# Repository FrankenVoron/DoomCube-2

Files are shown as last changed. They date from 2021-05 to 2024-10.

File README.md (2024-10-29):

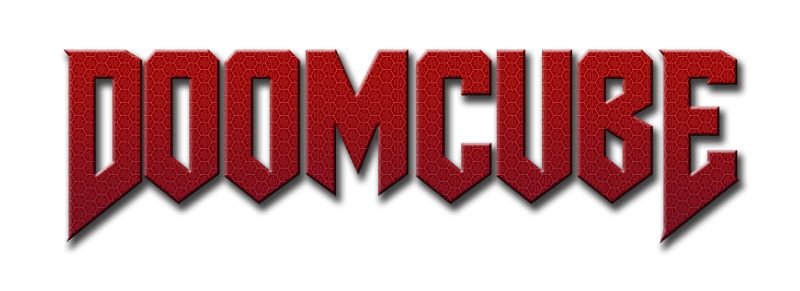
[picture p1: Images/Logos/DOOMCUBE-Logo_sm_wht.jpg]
DOOMCUBE

# Doom-Cube
A mod for Voron 2.4; designed by the Voron community, for the Voron community! Please note that it is a work in progress, design iterations are expected. The files are hosted on github so we have a log of the past history for the parts.



#### Key features:

- 4040 vertical components to allow for insulation with air gap stock

- Top mounted Z drives

- Top mounted low voltage components

- Bottom mounted high voltage components

#### Optional

- Replace X/Y cable chains with umbelical (Z chain retained for A/B motors and Y endstop)

#### Changes required:

- 4pcs 4040 extrusions (HFSB5-4040)   -or-   4pcs 404020 rounded extrusions (HFSR5-404020)

- New Z Idlers  (only printed parts required)

- Relocate X/Y endstops  (only printed parts required)

- Cable Glands for Umbelical

#### Tips for printing parts:

For any Voron stock parts, or the Z idlers, please use standard Voron settings.

For skirts, etc, you may use other settings to reduce filament usage. Currently I am using: 0.3mm layer height, 2 perimeters, 2 bottom, 3 top, 20% infill. 

## BOM 

All extrusions are listed using Misumi part numbers.

Part numbers are listed for both square 4040, and rounded 404020 vertical extrusions.  Choose only one type.  The first set of part numbers is for plain cut extrusions.  The second part number is for square extrusions that are cut and drilled by misumi.  

#### Note:
If you choose to use rounded corners, you will need to reuse your frame's existing 2020 vertical extrusions, or purchase a set of them for a scratch build.  The rounded verticals do not require machining, but the 2020 verticals that nest into them will need to have holes drilled to enable securing the rounded piece with blind joints, as shown here.

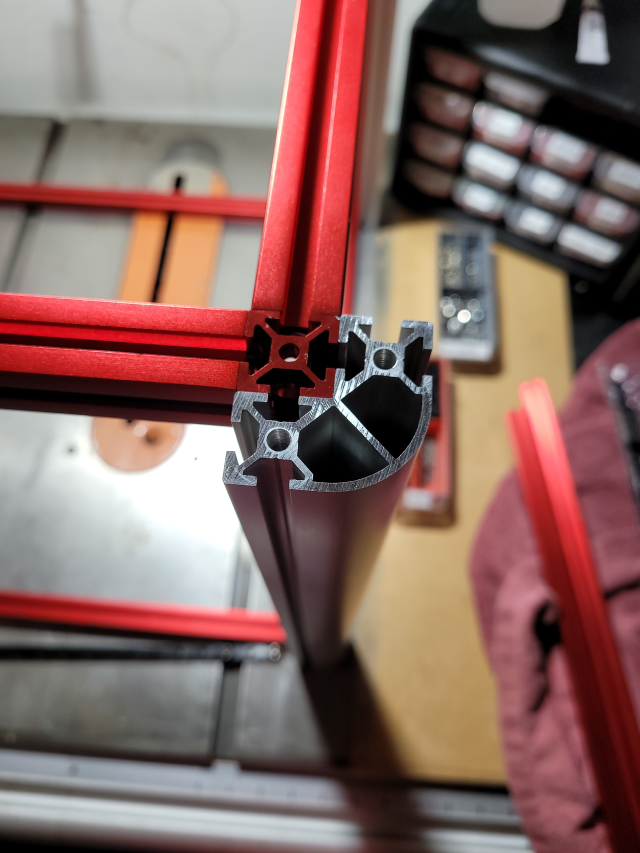
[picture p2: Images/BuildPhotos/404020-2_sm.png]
Corner extrusion profile shown from above


## Extrusions Based on Standard V2 Build Sizes

## DOOM-350
### Frame Extrusions
#### DIY
Misumi Part #  |Qty
|:----:|:----:|
Square Verticals: HFSB5-4040-530 |4 
Rounded Verticals: HFSR5-404020-530 |4

#### Pre-Drilled
Misumi Part #  |Qty
|:----:|:----:|
Square Verticals: HFSB5-4040-530-LCP-RCP |4

### Door Extrusions

#### DIY
Misumi Part #  |Qty
|:----:|:----:|
HFSB5-2020-530|2
HFSB5-2020-428|2

#### Pre-Drilled
Misumi Part #  |Qty
|:----:|:----:|
HFSB5-2020-530-AH10-BH520|2
HFSB5-2020-428-TPW|2

## DOOM-300
### Frame Extrusions
#### DIY
Misumi Part #  |Qty
|:----:|:----:|
Square Verticals: HFSB5-4040-480 |4
Rounded Verticals: HFSR5-404020-480 |4

#### Pre-Drilled
Misumi Part #  |Qty
|:----:|:----:|
Verticals: HFSB5-4040-480-LCP-RCP |4

### Door Extrusions
#### DIY
Misumi Part #  |Qty
|:----:|:----:|
HFSB5-2020-480|2
HFSB5-2020-378|2

#### Pre-Drilled
Misumi Part #  |Qty|
|:----:|:----:|
HFSB5-2020-480-AH10-BH470|2
HFSB5-2020-378-TPW|2

## DOOM-250
### Frame Extrusions
#### DIY
Misumi Part #  |Qty
|:----:|:----:|
Square Verticals: HFSB5-4040-430 |4
Rounded Verticals: HFSR5-404020-430 |4

#### Pre-Drilled
Misumi Part #  |Qty|
|:----:|:----:|
Square Verticals: HFSB5-4040-430-LCP-RCP| 4

### Door Extrusions

#### DIY
Misumi Part #  |Qty| 
|:----:|:----:|
HFSB5-2020-430|2
HFSB5-2020-328|2

#### Pre-Drilled

Misumi Part #  |Qty| 
|:----:|:----:|
HFSB5-2020-430-AH10-BH420|2
HFSB5-2020-328-TPW|2

## Door Hinges
Silver and Black are listed 

|Misumi Part #  |Qty|Color
|:---:|:---:|:---:|
HHPSN5-SET|2| Silver
HHPBSN5-SET|2| Black

# Ongoing and Future Development
While we all have many irons in the fire, Doomcube v2 is still being worked on.  Keep an eye out for changes coming to the panel printed parts, as well as some coming mods from the community.  In the interest of encouraging more Doom builds, as well as more mods, a complete DOOM CAD file is now available with all the Doom and Voron components together.  Find it in the CAD folder with all the individual component CAD files.  The individual components have been gone through and all hole sizes have been made consistent.  Missing chamfers were added, and some geometry cleaned up.  The frame and panel assemblies will stay as they are until new files are ready.
### CAD Notes
If you examine the complete CAD file you will see it is not limited to the basic DOOM and Voron components.  Included are two optional gantry variants, with a handful of popular community produced V2 mods installed.  The file is structured to be very easy to see what you want, and hide what you don't.  The step file has everything shown by default, so you'll need to hide the frame, skirts, and gantries you don't wish to see.  It should only take a few clicks.

DoomCubing is a great way to improve your v2.  It's also a perfect time to install several mods, while you have things partially disassembled.  To give you some ideas about possible mod combos, the optional modded gantries in the complete cad file contain the following excellent mods:

### Afterburner MGN12 Gantry
Mod|Repository
|:---:|:---:|
Ark's MGN12|https://github.com/VoronDesign/VoronUsers/tree/master/printer_mods/arkeet/mgn12
Hartk's GE5C Spherical Z Joint|[https://github.com/VoronDesign/VoronUsers/tree/main/printer_mods/hartk1213/Voron2.4_GE5C](https://mods.vorondesign.com/details/eB5T2RNQcYI4o6cilhpXEg)
Hartk's Pinmod (X/Y Joints, ,A/B Drive Frames, A/B idlers, Z idlers)|[https://github.com/hartk1213/MISC/tree/main/Voron%20Mods/Voron%202/2.4/Voron2.4_Pins_Mod](https://mods.vorondesign.com/details/C8XJJ0fBGfBFKQZctjKeA)

### Mantis MGN12 Gantry
Mod|Repository
|:---:|:---:|
Long's Mantis Toolhead|https://github.com/VoronDesign/VoronUsers/tree/master/printer_mods/Long/Mantis_Dual_5015
Hartk's GE5C Spherical Z Joint|[https://github.com/VoronDesign/VoronUsers/tree/main/printer_mods/hartk1213/Voron2.4_GE5C](https://mods.vorondesign.com/details/eB5T2RNQcYI4o6cilhpXEg)
Hartk's Pinmod (X/Y Joints, ,A/B Drive Frames, A/B idlers, Z idlers)|[https://github.com/hartk1213/MISC/tree/main/Voron%20Mods/Voron%202/2.4/Voron2.4_Pins_Mod](https://mods.vorondesign.com/details/C8XJJ0fBGfBFKQZctjKeA)
Phalanx's Other Idlers|https://github.com/selliott79/Other-V2-Idlers

### Other Mods
The following mods are present in all or most Doomcube variants in the complete CAD file.  Klicky is not on the Mantis toolhead, since it has a native magprobe that works identically to Klicky.

Mod|Repository
|:---:|:---:|
L.e.o.p.a.r.d and Hartk's Sexbolt Z Endstop|[https://github.com/hartk1213/MISC/tree/main/Voron%20Mods/Voron%202/2.4/Voron2.4_SexBolt_ZEndstop](https://mods.vorondesign.com/details/t1DBVlcUBbdEK6habEsVzg)
josar's Klicky Probe|https://github.com/jlas1/Klicky-Probe 
whoppingpochard's Gantry Rail Backers|https://github.com/tanaes/whopping_Voron_mods/tree/main/extrusion_backers

#### A big thanks to all original authors for permission to include their mods in the Doomcube CAD!  Always follow the links to their respective repos for the latest stl's, and info on how to best make use of their mods.

##### A set of stl checklists to match these mod sets is in the works.  That can be one of the most confusing parts of building up a modded printer from scratch, or doing many mods at once with redundant components.  Hopefully a few checklists will simplify things a little bit.  A huge debt is owed to all the mod makers and their willingness to share their work!  Keep up the good work y'all!

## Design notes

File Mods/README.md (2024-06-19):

# Mods

Printer mods for DOOMCUBE
Remember to update this README when uploading new mod!

## Table structure

Update the following table with the information about your mod:
- Your name
- A link to your sub-folder
- A short description of your mod

like so:
`
| Creator | [Mod title](link) | Description |`

---

| Creator | Mod title | Description |
| --- | --- | --- |
| crag-h4k | [direct drive z](./crag-h4k/direct-drive-z) |Replaces z motor assembly with a minimized direct drive z motor unit. |
| crag-h4k | [galileo adxl345 chain replacement](./crag-h4k/galileo-adxl345-chain-replacement) |Replaces the Galileo extruders's chain mount with a dedicated mount for a adxl345. |
| crag-h4k | [lil a drive cable cover](./crag-h4k/lil-a-drive-cable-cover) | Replaces beefy a-drive cable cover with a cute little cover - use with top mounted cable gland. |
| crag-h4k | [mgn12 galileo compatible cable gland mount](./crag-h4k/mgn12-galileo-cable-gland) | Simple cable gland mount for mgn12 x-axis mod and Galileo extruder. |
| crag-h4k | [z chain m12 gland ptfe anchor](./crag-h4k/z-chain-cable-gland-ptfe-anchor) | Simple a cable gland mount and 4mm PTFE tube pass-through for upper Z chain anchor - attempts to preserve z-axis build volume.  |
| mvieleers | [My Custom DoomCube-2](./mvieleers/my_doomcube) | 300m3 DoomCube-2 with several popular included and a few of my own mods. |
| mvieleers | [Schaffner FN-286 Plug Panel](./mvieleers/fn-286_plug_panel) | Modded Plug Panel to hold the Schafnner FN-286|
| mvieleers | [Corner Panel Mounts](./mvieleers/corner_panel_mounts)| Modded upper and lower corner caps and square feet to attach the top and bottom deck panels to the feet with magnets. |
| mvieleers | [Galileo ADXL345 Chain Replacement with Umbilical Mount](./mvieleers/adxl_mount_w_umbilical)| This mod is an alteration of crag-h4k's mod to replace the chain mount on a Galileo extruder with an adxl345 mount. The adxl345 mount has cutouts so an umbilical can be mounted to the adxl345 mount with tie-wraps.
| KayosMaker | [tip-in swing-in panels](./KayosMaker/Toolless%20Panel%20Mod) | Work In Progress - nothing now, just a frame generator and some shaved corner pieces.  will post the rest soon |
| MartinNYHC | [Slotted skirts with fan mount](./MartinNYHC/Slotted_Skirts_With_Fan_Mount) | 350m3 Doomcube slotted skirts with fan mount |
| TheSquiffy | [Side panels with more clearance](./TheSquiffy/Side_panels_with_more_clearance) | Side panels with more clearance for Doomcube |
| Maker Technologies | [Rounded Upper Corner Panel Mounts with Rubber Feet Support](./Maker_Technologies/Upper%20Rounded%20Corner%20Panel%20holder%20with%20Support%20for%20Rubber%20Feet) | Keeps the Top panel in place while adding a spot to insert rubber feet on the top corners.|
| Maker Technologies | [Rounded Lower Corner Panel Mounts](./Maker_Technologies/Lower%20Rounded%20Corner%20Panel%20Holder) | Keeps the bottom panel in place.|
| Maker Technologies | [BTT Pi TFT70 Mount](./Maker_Technologies/Pi%20Tft70%20Skirt%20Mount) | A mount for a BTT Pi TFT70 to attach to a skirt.|
| k3vOOoOO | [https://www.printables.com/model/604933-doomcube-dual-power-switch-plate](https://www.printables.com/model/604933-doomcube-dual-power-switch-plate)| Dual BOM-spec rocker switches and filtered inlet. |

---

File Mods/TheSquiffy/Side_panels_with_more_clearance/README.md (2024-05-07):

**Side panels with more clearance for DoomCube**

Original panel's distance it's set around 1.6mm, this sometimes gives few clearance for gantry's belts to move, scratching the panels and causing some noise during operation.

The purpose of this mod it's to reduce distance between the side panels from ~9.6mm down to 3.5mm, leaving up to 7mm clearance for belts.

This mod could also be applied to back panels even though it's not strictly necessary.

The design fills gaps between the extrusion bars and panels to avoid having small channels where dirt could end up.

I have personally installed to my DoomCube 250 and made 300 and 350 stl files but I couldn't test them directly.

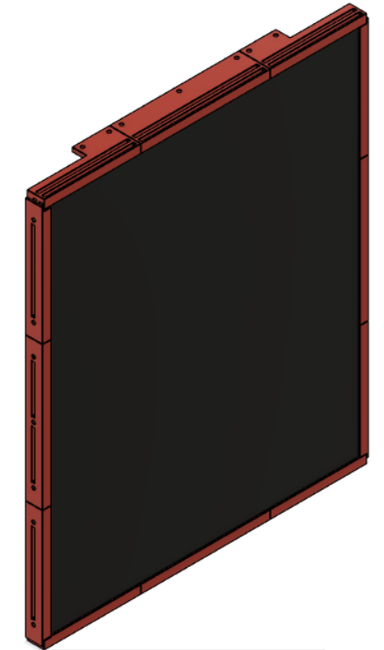
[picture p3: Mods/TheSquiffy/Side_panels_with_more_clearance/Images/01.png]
||
-

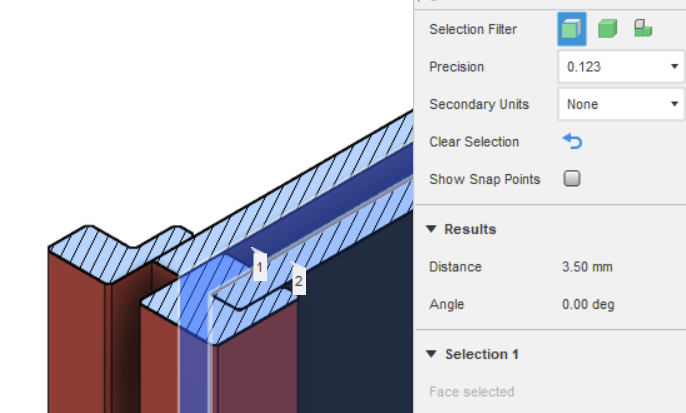
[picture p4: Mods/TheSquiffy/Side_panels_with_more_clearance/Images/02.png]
||
-

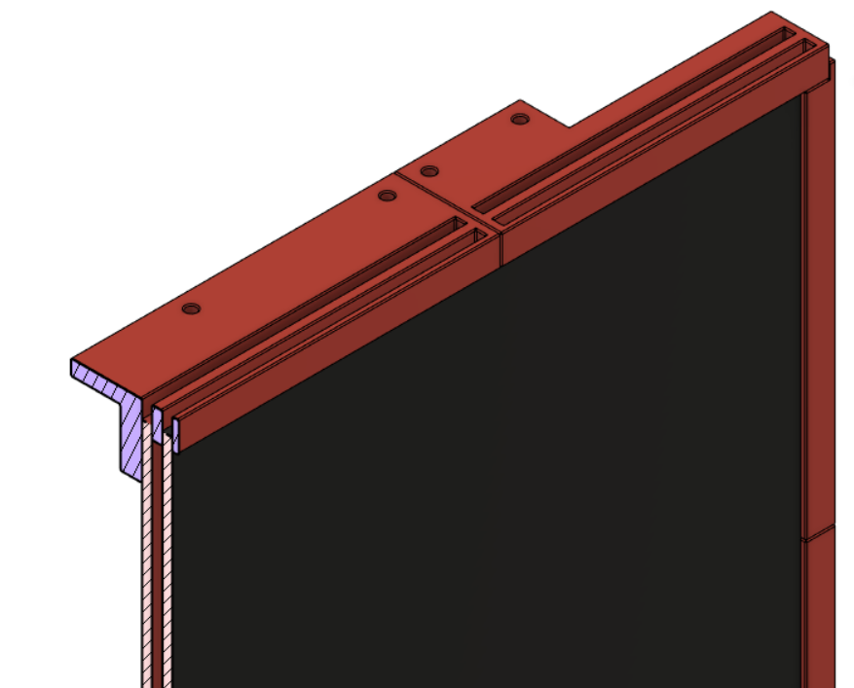
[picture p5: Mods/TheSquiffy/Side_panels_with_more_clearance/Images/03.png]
||
-

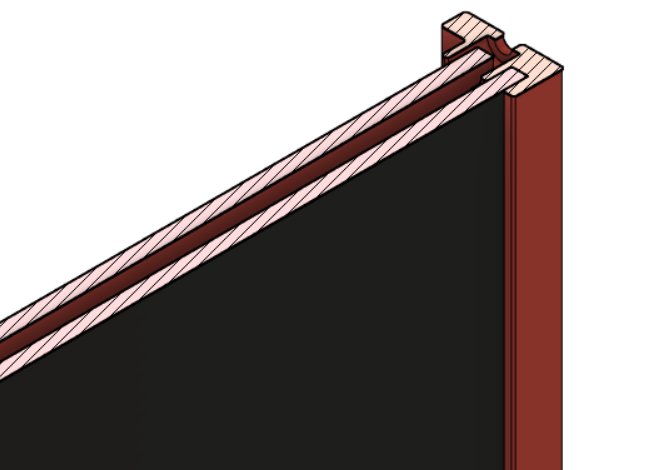
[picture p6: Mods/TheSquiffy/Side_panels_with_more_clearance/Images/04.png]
||
-

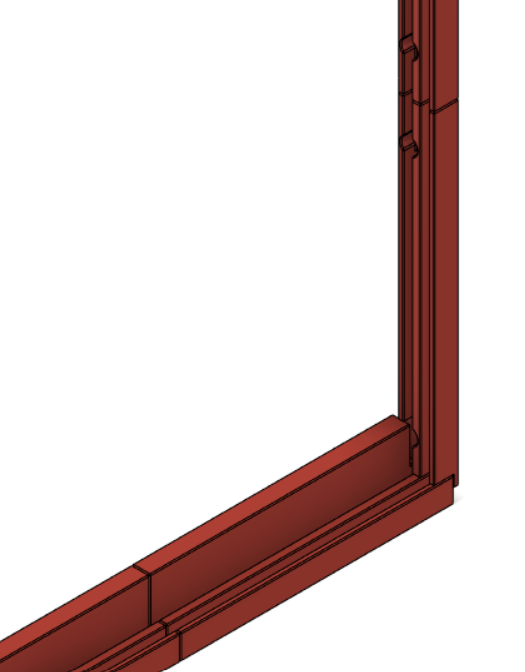
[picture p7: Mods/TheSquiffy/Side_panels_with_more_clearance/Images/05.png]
||
-

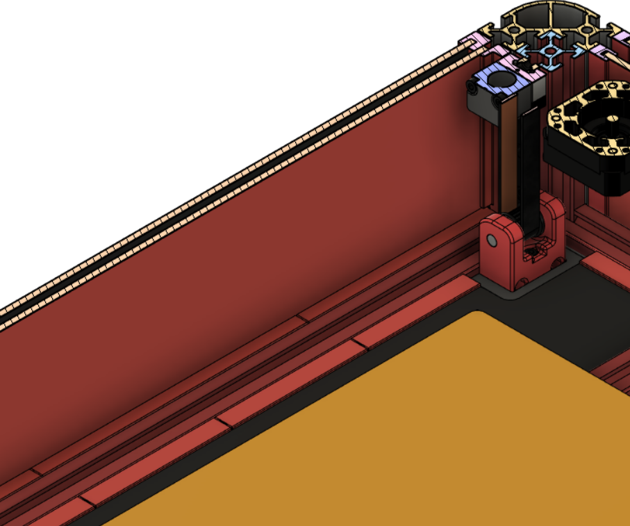
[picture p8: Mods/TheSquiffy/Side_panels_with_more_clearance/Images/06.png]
||
-

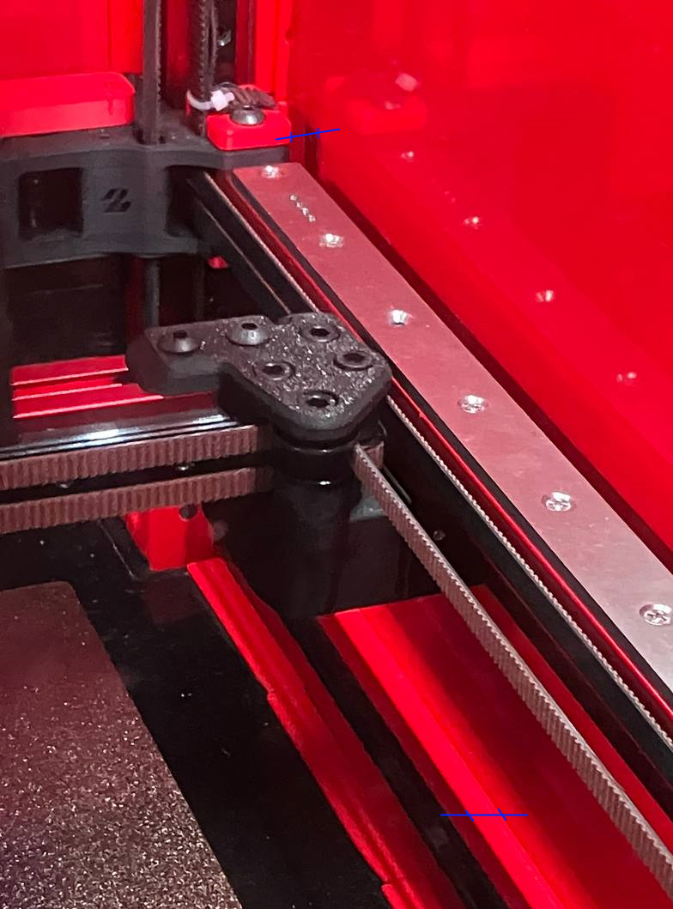
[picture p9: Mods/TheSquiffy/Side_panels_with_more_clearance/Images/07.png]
||
-

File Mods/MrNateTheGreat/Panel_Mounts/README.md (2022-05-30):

Magnetic clipping Doomcube V2 top/bottom panel attachment that allows for top and bottom panel installation after frame assembly.

GOALS: 
No loss of compatability with already cut panels
V0 Printable as the top/bottom panels are necessary to build printer but side panel mounts can be printed later.
Be multi-size compatible

STLs already in print orientation.  There is a 3.25mm bridge for the upper clips but should not require supports. Line width needs to be 0.4mm or lower for bridging to slice properly.

Uses 32 6x3mm magnets per panel set, so 64 magnets total.  

All parts should be printable on a V0.  The 350mm middle clips would need to be rotated 45 degrees to fit on V0 bed.
DOOM Mag Panels 3
DOOM Mag Panels 4
DOOM Mag Panels 1
DOOM Mag Panels 2

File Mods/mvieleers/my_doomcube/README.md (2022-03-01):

# DoomCube
Based on the DoomCube Mod for the Voron V2 and several popular Mods out there, I decided to capture my personalized DoomCube build in a full CAD.

This repository will list any Mods used that deviate from the regular Voron V2.4 and DoomCube build.

Different types of Mods are used in this build:
- Personal DoomCube modifications. These are the deviations from the original DoomCube files. **Please note: the modifications are specific to this particular build which is a 300m3 build. Be very carefull if you use these files and make sure they can be applied to your situation.** The files will be hosted under this "My DoomCube" Mod. You can find the files under [STL](STL)
- Official Mods. These are official Mods for the Voron V2.4 and DoomCube and are untouched by me and implemented as is. I will link to their official github where you will need to download the files relevant for you.
- Altered DoomCube specific Mods. These are Mods by me based on the official DoomCube files and applicable to any DoomCube build. They will be hosted seperately under the [Mods section of the official DoomCube repository](../..). You will need to download the files from their own mod repository.
- Voron V2 Mods by me. These are Mods by me that are applicable to any Voron V2 (Doomed or not) and will be hosted from my [own Github](https://github.com/mvieleers/Voron-V2) where you can download the files.

**If I don't specify a part, it means that you will need to download the STL from the [Original DoomCube repository](https://github.com/FrankenVoron/DoomCube-2), or in case the part is not listed there as well, from the original [Voron 2 repository](https://github.com/VoronDesign/Voron-2).**

[Make sure to join the DoomCube discord!](https://discord.gg/EAANfEk25f)

The DoomCube should be capable of reaching chamber temperatures of 70 degrees and higher. 
I was able to reach 70 degrees inside the chamber, having the DoomCube sit in a garage where the ambiant temperature was 5 degrees Celcius.
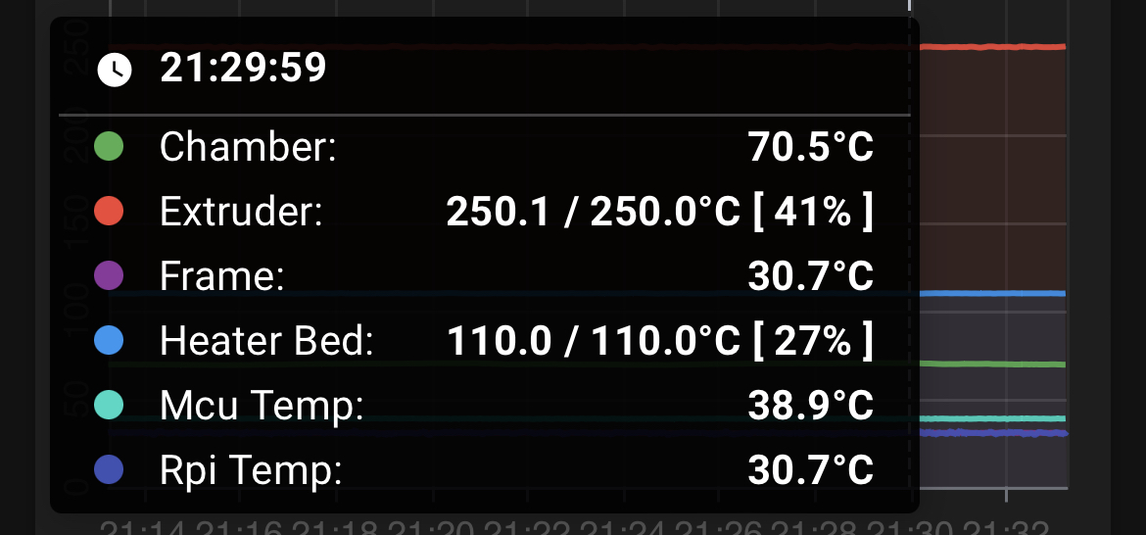
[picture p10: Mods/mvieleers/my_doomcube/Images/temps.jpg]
Temps


## CAD
A full CAD for this build will is available. For the most part it will include fasteners as well, with the exception for flanges, skirts and panelmounts.
As the CAD is 100 Mb+ it cannot be uploaded as one into Github. I've broken it up in different sections (one of these also needed to be zipped). When you import the STEP files into a new drawing, it will form one complete assembly again.

Click [HERE](CAD) for STEP files

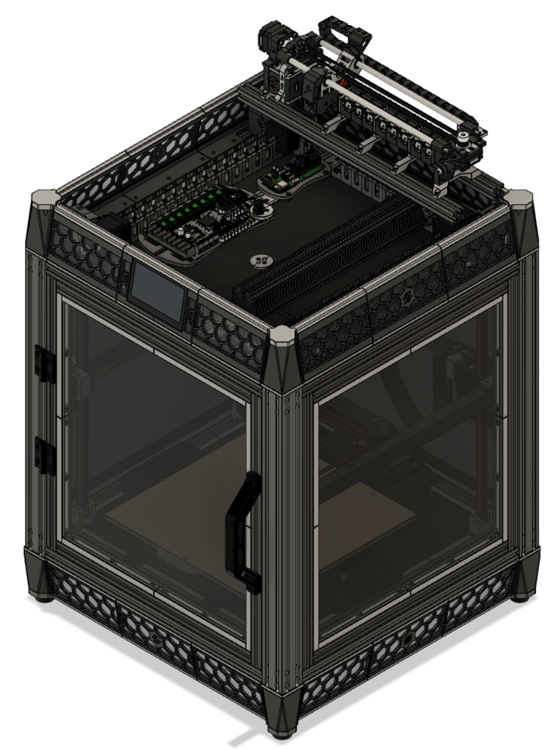
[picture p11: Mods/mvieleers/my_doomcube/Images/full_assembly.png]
Full Assembly


## Frame

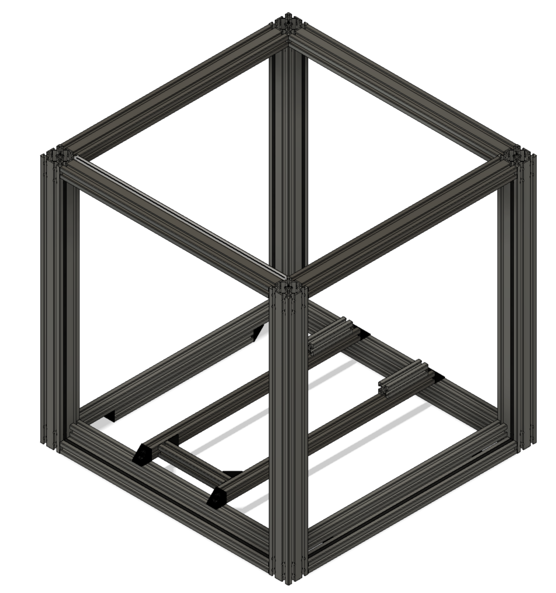
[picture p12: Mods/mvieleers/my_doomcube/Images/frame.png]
Frame


### Specifics
- 300m3 build.
- I'm using 20mm taller vertical 4040s, so the door, side and back panels all rest within an extrusion frame. This eliminates the need for the flanges to support the panels.
- Instead of 2020's for the top frame, I'm using 4020's.
- Instead of single 2020's for the bottom frame, I'm using double 2020's in the bottom frame in order for the panels to rest on top of the additional 2020 extrusion.
- The bed frame has a cross bar in order to mount my magbed with 3 mounting points instead of 4. I'm using the Mandala Rose Works Kinematic Mounting set. Because the mounting set adds some z height to the bed, there's a 8cm extrusion in the back on both bed extrusions to be able to raise the z-endstop and purge bucket.
- I'm using slot covers to seal any gaps between the frame and the side panels. The slot covers are also intended to keep the panel in place. In order for this to work the slot cover need to protrude above the extrusion. Misumi HSCKS5 slot covers will not work for this goal as they sit completely flush with the extrusion. I've found that Aliexpress slot covers work well for this.
- The CAD shows slot covers on all 4 sides of the frame where the panel is placed. If you actually use slot covers on all 4 sides, you will have the best seal of any gaps, but removing the panel later will require a lot of force. I've found that using slot covers on 3 sides works best. It still makes a good seal and you'll be able to fairly easy push the entire panel out when you require them of for maintenance or printing pla.

### Hardware
Section|Part| Part #|QTY|Remarks
|:---:|:----:|:----:|:---:|:---:|
Bottom Frame
||Bottom Horizontals|[HFSB5-2020-420-TPW](https://uk.misumi-ec.com/vona2/detail/110302683830/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)|10|Can be reused if you're converting from a standard V2 300
||Bottom Horizontals|[HFSB5-2020-280-TPW](https://uk.misumi-ec.com/vona2/detail/110302683830/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)|2|Can be reused if you're converting from a standard V2 300
||OpenBuilds Angle Corner Connector|[20x20x20](https://openbuildspartstore.com/black-angle-corner-connector/)|4|Used to keep the two extrusions from rotating
||Slot Covers|[DCR6-2020](https://nl.aliexpress.com/item/1005001664501395.html?spm=a2g0s.9042311.0.0.27424c4dtVOEhL)|1m|Comes in 10m so needs to be cut to length.
Vertical Frame
||Square Verticals|[HFSB5-4040-500-LWP-RWP-TPW](https://uk.misumi-ec.com/vona2/detail/110302684530/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)|4
||Slot Covers|[DCR6-2020](https://nl.aliexpress.com/item/1005001664501395.html?spm=a2g0s.9042311.0.0.27424c4dtVOEhL)|2m|Comes in 10m so needs to be cut to length.
Top Frame
||Top Horizontals|[HFSB5-2040-420-TPW](https://uk.misumi-ec.com/vona2/detail/110302684350/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)|4
||Slot Covers|[DCR6-2020](https://nl.aliexpress.com/item/1005001664501395.html?spm=a2g0s.9042311.0.0.27424c4dtVOEhL)|1m|Comes in 10m so needs to be cut to length.
Bed Frame
|||[HFSB5-2020-420-TPW](https://uk.misumi-ec.com/vona2/detail/110302683830/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)|2|Can be reused if you're converting from a standard V2 300
|||[HFSB5-2020-130](https://uk.misumi-ec.com/vona2/detail/110302683830/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)|1
||OpenBuilds Angle Corner Connector|[20x20x20](https://openbuildspartstore.com/black-angle-corner-connector/)|6|4 for securing the bed frame to the bottom frame, 2 to secure the cross bar. 4 can be reused if you're converting from a standard V2
|||[HFSB5-2020-80](https://uk.misumi-ec.com/vona2/detail/110302683830/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)|2|Please note that you'll have to drill 2 4mm holes in each extrusion to be able to bolt these extrusions to the normal bed extrusions using 2x M5x6 BHCS. I have drilled these holes roughly 2cm from the end, but you can basically drill them anywhere.

## Panels

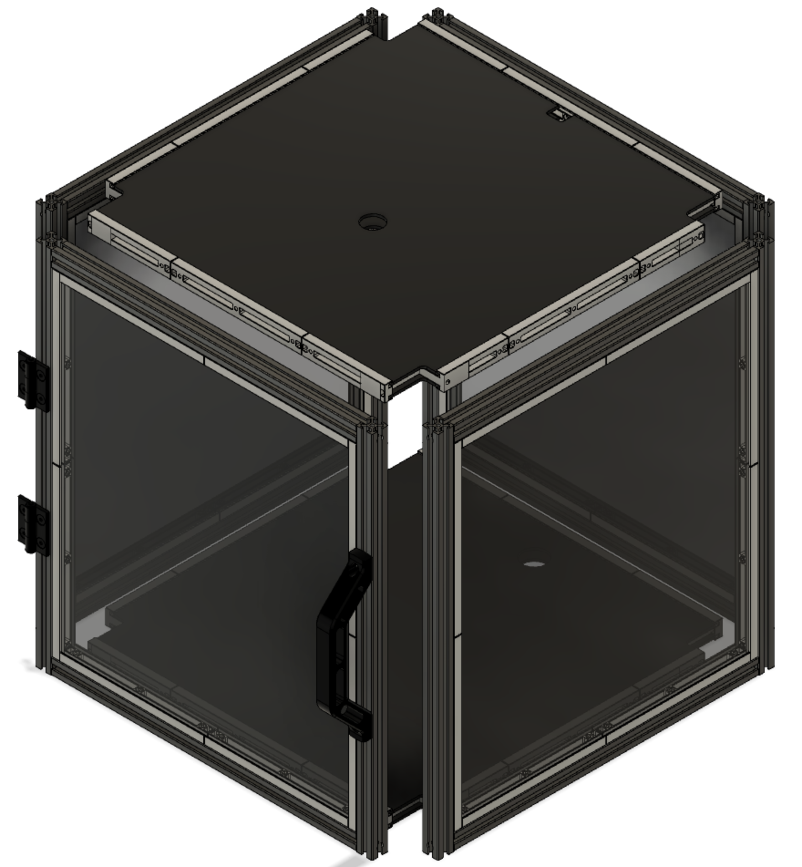
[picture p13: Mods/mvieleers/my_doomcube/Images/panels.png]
Panels


### Specifics
- The principle of the original DoomCube door is applied to the side and back panels, where the panels slide into panelmounts that bolt into the extrusion. This method is copied to all the sides. For my 300 build I went with 2 pieces per extrusion though. Please check whether you can fit these on your build plate if printing this on a small printer.
- The slot covers (see frame section) should create a good seal and a tight fit, which should make the panels to securely stay in place. If this is not the case, I have modded the excellent [Annex Engineers Panel Clips for 2020 extrusions](https://github.com/Annex-Engineering/Annex-Engineering_Other_Printer_Mods/tree/master/All_Printers/Annex_Panel_2020_Clips_and_Hinges/panel_clips_and_corners). The Mod involves flattening the clips so it sits flush with the side panel frame. Please take note of the [Annex Engineering EULA](STL/Panels/Panel%20Clips/LICENSE.md)
It looks like the misumi slot covers might sit too flat in the extrusion. Aliexpress slot covers stick out more and might make a better fit. Will provide final results when I finish the build.
- Top and bottom panels use the "standard" Doomcube panelmounts, but the corners have been modded to include the part that goes in between the panels (from [Kayosmaker's mod](https://github.com/FrankenVoron/DoomCube-2/tree/main/Mods/KayosMaker/Toolless%20Panel%20Mod/Panel%20Frame%20Generator%20WORK%20IN%20PROGRESS). This should add to the stability.
- Top and bottom (deck) panels have cutouts for wire passthroughs and the top deck panel has mounting holes for mounting the ERCF on top of the top deck panel.

### Dimensions
Drawings are [here](Drawings), DXFs are [here](DXF)

Panel|Drawing|DXF|QTY
|:---:|:---:|:---:|:---:|
Door|panel_side.pdf|panel_side.dxf|2
Sides|panel_side.pdf|panel_side.dxf|4
Back|panel_back.pdf|panel_side.dxf|2
Top|panel_top.pdf|panel_top.dxf|2
Bottom|panel_bottom.pdf|panel_bottom.dxf|2
Top Deck|panel_top_deck.pdf|panel_top_deck.dxf|1
Bottom Deck|panel_bottom_deck.pdf|panel_bottom_deck.dxf|1

### Printed Parts
Section|Part|STL Origin|QTY
|:---:|:---:|:---:|:---:|
Door / Side / Back Panel Mounts
|Horizontal piece|[This Mod](STL/Panels/Sides)|16
|Vertical piece|[This Mod](STL/Panels/Sides)|16
|Corner Panel Clips|[This Mod](STL/Panels/Panel%20Clips)|16 (optional)
|Center Panel Clips|[This Mod](STL/Panels/Panel%20Clips)|16 (optional)
|Key for Corner and Center Panel Clips|[Annex Engineering Offical](https://github.com/Annex-Engineering/Annex-Engineering_Other_Printer_Mods/blob/master/All_Printers/Annex_Panel_2020_Clips_and_Hinges/panel_clips_and_corners/key/STL/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)|36 (optional)
Top / Bottom Panel
|Straight center piece|[This Mod](STL/Panels/Top_Bottom)|8
|Corner piece 1|[This Mod](STL/Panels/Top_Bottom)|4
|Corner piece 2|[This Mod](STL/Panels/Top_Bottom)|4
|Corner piece 1 mirrored|[This Mod](STL/Panels/Top_Bottom)|4
|Corner piece 2 mirrored|[This Mod](STL/Panels/Top_Bottom)|4

### Hardware
Hardware|Part|QTY|Remarks
|:---:|:---:|:---:|:---:
Vertical extrusions|[HFSB5-2020-458-LCH-RCH](https://uk.misumi-ec.com/vona2/detail/110302683830/?HissuCode=HFSB5-2020-458-LCH-RCH)|8
Horizontal extrusions|[HFSB5-2020-378-TPW](https://uk.misumi-ec.com/vona2/detail/110302683830/?HissuCode=HFSB5-2020-378-TPW)|8
Handle|[Aluminum Alloy Door Handle](https://nl.aliexpress.com/item/1407596513.html?spm=a2g0s.9042311.0.0.66fb4c4deTZEmA)|1|CAD shows printed door handle, I use this type of aluminum handle in size 120mm (ordered without screws and nuts)
Hinge|[HHPBSN5-SET](https://uk.misumi-ec.com/vona2/detail/110302362010/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)|2

## Skirts

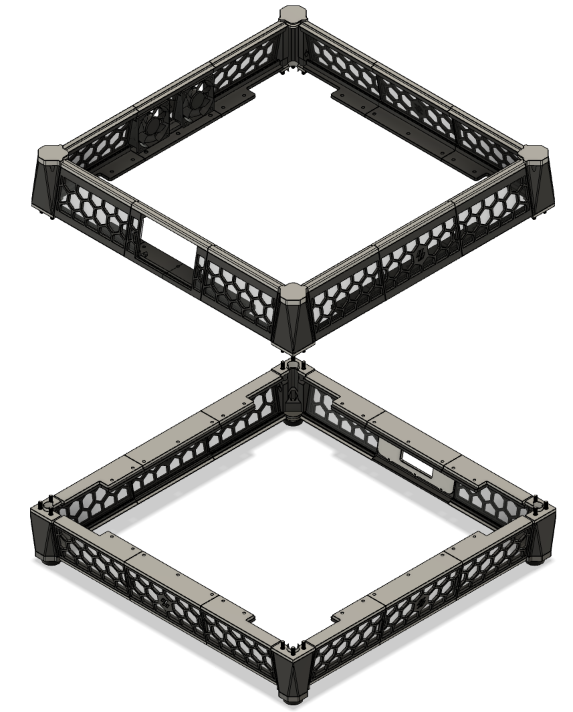
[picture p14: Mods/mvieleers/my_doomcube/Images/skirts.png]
Skirts


### Specifics
- Basis is the hexagon skirts from the original DoomCube. 
- Due to side and back panel mounting system, flanges of the door are used all around as well as the panelmounts.
- Panelmounts are 2 pieces per side, instead of 3. This might not be printable on smaller bed sizes.
- Top and Bottom have altered top caps for the corners. These caps allow the deck panels to be attached to the corners with magnets.
- Top corners and skirts have been increased in size in order to accomodate my Waveshare 4,3" LCD. For this a center skirt was modded to hold the LCD.

### Dimensions
Drawings are [here](Drawings), DXFs are [here](DXF)

Panel|Drawing|DXF|QTY
|:---:|:---:|:---:|:---:|
Bottom Center Skirt Panel|skirt_bottom_center.pdf|skirt_bottom_center.dxf|3
Bottom Side Skirt Panel|skirt_bottom_side.pdf|skirt_bottom_side.dxf|8
Top Center Skirt Panel|skirt_top_center.pdf|skirt_top_center.dxf|3
Top Side Skirt Panel|skirt_top_side.pdf|skirt_top_side.dxf|8
Top LCD Skirt Panel|skirt_top_lcd.pdf|skirt_top_lcd.dxf|2
Top Fan Skirt Panel|skirt_top_fan.pdf|skirt_top_fan.dxf|1

### Printed Parts
Section|Part|STL Origin|QTY
|:---:|:---:|:---:|:---:|
Square Corners Foot
||Bottom Corner|[Corner Panel Mounts](../corner_panel_mounts/STL)|4
||Top Corner|[This Mod](STL/Skirts/Corners/Top)|4
||Foot Mount (to extrusion)|[Original](../../../STLs/Corners/Square%20Extrusions)|8
||Bottom Corner Cap (panel mount)|[Corner Panel Mounts](../corner_panel_mounts/STL)|4
||Top Corner Cap (panel mount)|[This Mod](STL/Skirts/Corners/Top)|4
Skirts
||Bottom Center Skirt|[This Mod](STL/Skirts/Skirts/Bottom)|3
||Bottom Left Side Skirt|[This Mod](STL/Skirts/Skirts/Bottom)|4
||Bottom Right Side Skirt|[This Mod](STL/Skirts/Skirts/Bottom)|4
||Bottom Power Inlet Skirt|[FN-286 Plug Panel](../fn-286_plug_panel)|1
||Bottom Power Inlet Skirt Inlay|[FN-286 Plug Panel](../fn-286_plug_panel)|1
||Top Center Skirt|[This Mod](STL/Skirts/Skirts/Top)|2
||Top Left Side Skirt|[This Mod](STL/Skirts/Skirts/Top)|4
||Top Right Side Skirt|[This Mod](STL/Skirts/Skirts/Top)|4
||Top LCD Skirt|[This Mod](STL/Skirts/Skirts/Top)|1
||Top Fan Skirt|[This Mod](STL/Skirts/Skirts/Top)|1
Flanges
||Center Flange|[This Mod](STL/Skirts/Flanges/)|8
||Side Flange|[This Mod](STL/Skirts/Flanges/)|16
Skirt Accents
||Center Skirt Accent|[Original](https://github.com/FrankenVoron/DoomCube-2/tree/main/STLs/Skirts/Hexagon%20Skirts)|7
||Left Side Skirt Accent|[Original](https://github.com/FrankenVoron/DoomCube-2/tree/main/STLs/Skirts/Hexagon%20Skirts/300)|8
||Right Side Skirt Accent|[Original](https://github.com/FrankenVoron/DoomCube-2/tree/main/STLs/Skirts/Hexagon%20Skirts/300)|8

### Hardware
Hardware|Part|QTY|Remarks
|:---:|:---:|:---:|:---:
4.3" LCD|[Waveshare 4.3" LCD DSI](https://www.waveshare.com/4.3inch-dsi-lcd.htm)|1|The Raspberry Pi can be screwed to the LCD screen
Power Inlet|[Schaffner FN-286](https://www.digikey.nl/product-detail/en/schaffner-emc-inc/FN286-1-06/817-1928-ND/1997125?productid=1997125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)|1

## Heated Bed

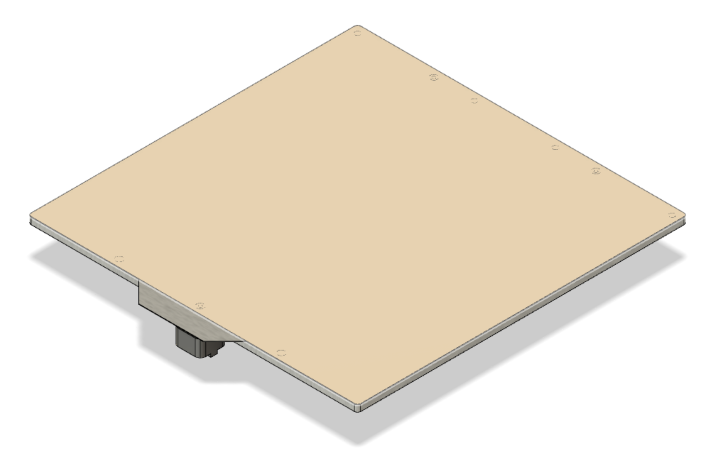
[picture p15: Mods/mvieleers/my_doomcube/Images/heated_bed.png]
Heated Bed


### Specifics
- Mandala Rose Works ultra flat magbed is used. It has mounting holes for both the V1.8 and the V2.4. Therefor I'm able to use a triangle 3-point mounting method, by inserting a cross bar between the two bed extrusions. This is also done to accomodate for a kinematic mounting system that is has been released by Mandala Rose Works.
- When not using a kinematic mounting solution, you will only need 3 of the original knurled knuts

### Hardware
Hardware|Part|QTY|Remarks
|:---:|:---:|:---:|:---:
Mic6 Bed|[Mandala Rose Works Ultra Flat Bed](https://www.mandalaroseworks.com/shop/voron/voron-300-standard-bed)|1|
Heater|[Keenovo 240x240 600W 220V](https://keenovo.store/collections/standard-keenovo-silicone-heaters/products/keenovo-square-silicone-heater-3d-printer-build-plate-heatbed-heating-pad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)|1
Magnetic Sheet|[Graviflex 310x310](https://fermio.xyz/en/mechanical/magnetic-sheets/121/magnetic-sheet-310x310x1mm)|1|Only when not using a magbed
Spring Steel Plate|[300x300 Spring Steel Plate](https://www.vonwange.com/product/300x300mm-1-4310-spring-steel-plate/)|1|
PEI Sheet|[Buildtak 12x12" PEI](https://www.buildtak.com/product/buildtak-3d-printing-surface-pei/)|1|
Knurled Nuts|Voron Standard Knurled Nuts|3|Only when not using the kinematic bed mounts
Kinematic Bed Mounts|[Matched Height Kinematic Set](https://www.mandalaroseworks.com/shop/voron/matched-height-kinematic-kit)|1|When using the kinematic bed mounts you will need to use a 35mm sexbolt for your Z Endstop to accommodate for the height difference.

## Z-Assembly

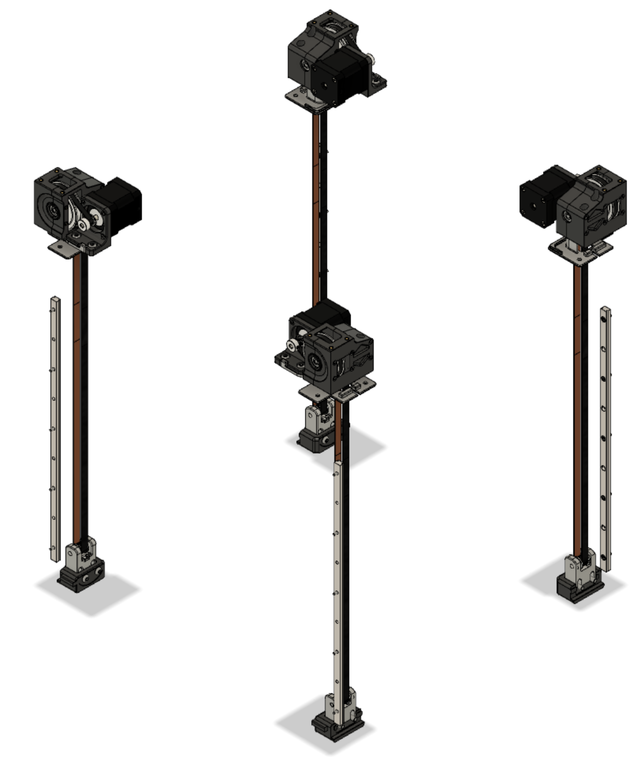
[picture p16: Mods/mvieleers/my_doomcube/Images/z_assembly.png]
Z Assembly


### Specifics
- Z-Drives are completely original DoomCube
- Motor Mounts are taken from the DoomCube CAD, there are no stl's for this in the repository which implies to use the original V2.4 parts. Those have 3 mounting points though, I like the 4 mounting points better, so I created the stl from the DoomCube CAD.
- The belt covers are modded from the original non-reflectix belt covers, I just added a somewhat different ledge to make a tighter integration to the panels.
- I'm using the 9mm pinned Z-Idlers

Section|Part|STL Origin|QTY
|:---:|:---:|:---:|:---:|
Z-Drive
||Z-Drive Main|[Original](https://github.com/FrankenVoron/DoomCube-2/tree/main/STLs/Z_Drives)|2 standard, 2 mirrored
||Z-Drive Retainer|[Original](https://github.com/FrankenVoron/DoomCube-2/tree/main/STLs/Z_Drives)|2 standard, 2 mirrored
Motor Mount
||Motor Mount|[This Mod](STL/Z-Assembly/Z-Drives)|2 standard, 2 mirrored
Z-Idler
||Belt Tensioner 9mm pinned|[Original](https://github.com/mvieleers/DoomCube-2/tree/main/STLs/Z_Idlers)|4
||Tensioner bracket|[Original](https://github.com/mvieleers/DoomCube-2/tree/main/STLs/Z_Idlers)|2 standard, 2 mirrored
Belt Cover
|| Belt Cover|[This Mod](STL/Z-Assembly/Belt%20Covers)|2 standard, 2 mirrored

## Gantry

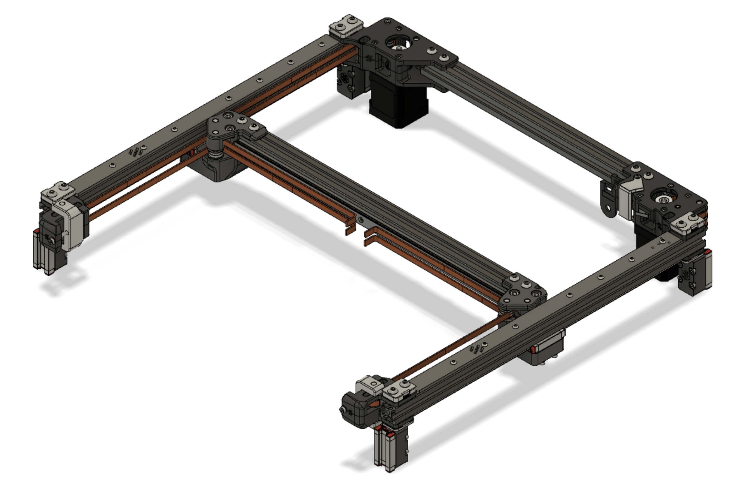
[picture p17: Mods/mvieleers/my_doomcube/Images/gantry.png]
Gantry


### Specifics
The Gantry is a combination of several official Mods. Take good care to select the correct versions from each Mod so they work together.
**Due to using the MGN12 mod in combination with the Gantry Backing Plates Mod and the Y Endstop Relocation Mod, the Y-endstop will trigger to soon due to the added backer. Therefor I've included a modded upper part for the A-drive with the Y endstop mounting point 3mm recessed.**
|Mod|Creator|
|:---:|:---:|
|[MGN12 X axis](https://github.com/VoronDesign/VoronUsers/tree/master/printer_mods/arkeet/mgn12)|arkeet
|[Pins Mod](https://github.com/VoronDesign/VoronUsers/tree/master/printer_mods/hartk1213/Voron2.4_Pins_Mod)|hartk1213
|[Y Endstop Relocation](https://github.com/VoronDesign/VoronUsers/tree/master/printer_mods/hartk1213/Voron2.4_Y_Endstop_Relocation)|hartk1213
|[Upper part A-drive (pinned with Y-endstop 3mm recessed)](STL/Gantry/AB_Drive_Units)|mvieleers
|[GE5C](https://github.com/hartk1213/MISC/tree/main/Voron%20Mods/Voron%202/2.4/Voron2.4_GE5C/STLs)|hartk1213
|[Gantry Backing Plates](https://github.com/VoronDesign/VoronUsers/tree/master/printer_mods/whoppingpochard/extrusion_backers)|whoppingpochard
|[lil a drive cable cover](https://github.com/mvieleers/DoomCube-2/tree/main/Mods/crag-h4k/lil-a-drive-cable-cover)|crag-h4k

### Hardware
There are no deviations from the standard Voron V2 in terms of extrusions.

## X-Carriage

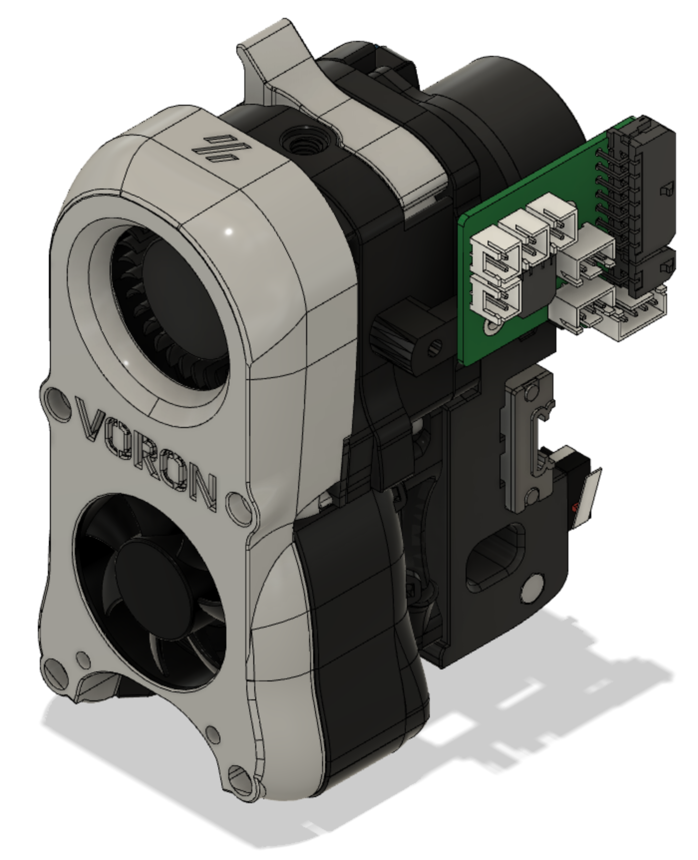
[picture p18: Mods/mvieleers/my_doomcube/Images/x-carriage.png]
X-Carriage


### Specifics
Like the Gantry, the X-Carriage is a combination of several official Mods. Again, take good care to select the correct STL's that work with your setup.
|Mod|Creator|
|:---:|:---:|
|[BlueDragonX's Klicky Mods-Voron 2.4 Direct Mount MGN12 X Carriage](https://github.com/jlas1/Klicky-Probe/tree/main/Usermods/bluedragonx)|bluedragonx
|[Galileo Clockwork](https://github.com/JaredC01/Galileo)|JaredC01
|[AB-BN-30](https://github.com/VoronDesign/VoronUsers/tree/master/printer_mods/Badnoob/AB-BN)|Badnoob
|[Simple mount for Hartk board for galileo.](https://github.com/VoronDesign/VoronUsers/tree/master/printer_mods/Majarspeed/Hartk_Mount_Galileo)|Majarspeed
|[Afterburner Toolhead Board - ERCF version](https://github.com/hartk1213/MISC/tree/main/PCBs/Afterburner_Toolhead_PCB)|hartk1213
[Galileo ADXL345 Chain Replacement with Umbilical Mount](../adxl_mount_w_umbilical)|mvieleers

### Printed Parts
The CAD contains the Galileo Clockwork body. In reality I am using the non-released version of the ERCF 1.1 filament sensor which replaces the Galileo Clockwork body. This STL circulates in the Enraged Rabbit Channel on Discord, but as it is not officially released, I will not provide it in this repository yet. It will be released together with the new ERCF 1.1 version. Please keep an eye out on the official and amazing [Enraged Rabbit Project](https://github.com/EtteGit/EnragedRabbitProject) for more information.
 
### Hardware
I'm using a Phaetus Dragon High Flow hotend with a bondtech CHT® Coated Brass 0.4 Nozzle.
Optionally you can select a Mosquito standard flow hotend.

## Other

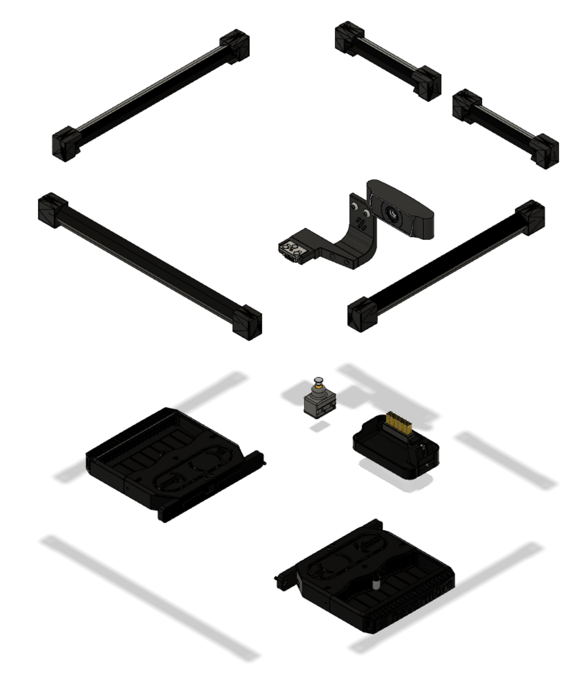
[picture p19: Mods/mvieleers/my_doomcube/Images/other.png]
Other


### Specifics
This section contains several additional Mods to complete the setup within the chamber
|Mod|Creator|Remarks
|:---:|:---:|:---:|
|[SexBolt Z endstop](https://github.com/hartk1213/MISC/tree/main/Voron%20Mods/Voron%202/2.4/Voron2.4_SexBolt_ZEndstop)|hartk1213|
|[Klicky-Probe](https://github.com/jlas1/Klicky-Probe)|jlas1 a.k.a. JosAr
|[Purge brush bucket](https://github.com/Annex-Engineering/Annex-Engineering_Other_Printer_Mods/tree/master/All_Printers/Purge_Brush_Bucket)|Annex Engineering
|[Nevermore Micro V5 Duo](https://github.com/0ndsk4/VoronUsers/tree/0ndsk4/printer_mods/0ndsk4/Nevermore_Air_Filter/Nevermore_Micro)|0ndsk4
|[Angry Led Mount](https://github.com/VoronDesign/VoronUsers/tree/master/printer_mods/42bios/LED_mount)|42bios
|[USB Camera Mount](https://github.com/VoronDesign/VoronUsers/tree/master/printer_mods/Takuya/USBCameraMount)|Takuya

### Hardware
Hardware|Part|QTY|Remarks
|:---:|:---:|:---:|:---:
Led Bar|[LumenTEC LT3 Profile](https://lumentec.eu/Aluminium-Eckig-LED-Profil-100cm-45-fuer-8-12mm-LED-Streifen-Profil-LT3-Abdeckung)|2|
USB Camera|[Wansview 1080p Webcam](https://www.wansview.com/cn/proinfo.aspx?proid=37&categoryid=3&aids=1)|1

## Electronics

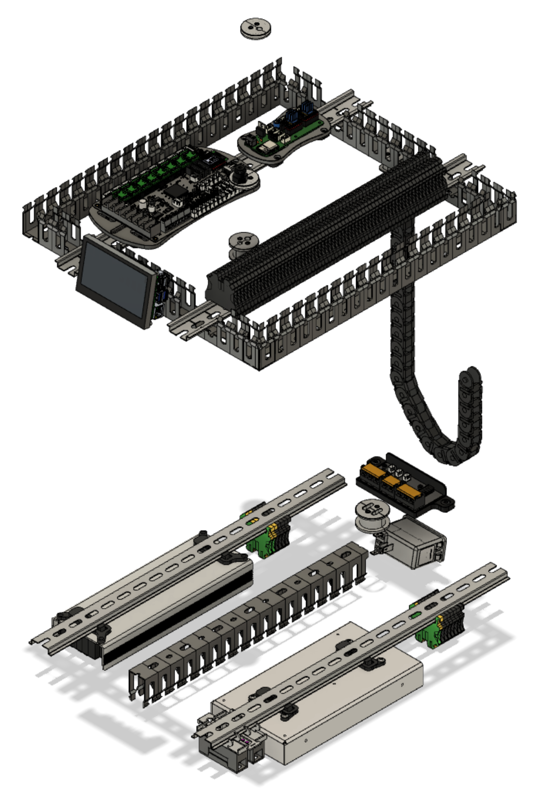
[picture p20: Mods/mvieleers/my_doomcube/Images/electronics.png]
Electronics


### Specifics
- I'm using 5 wire grommets for the passthrough of wires and the reverse bowden tube through the panels. The wire grommets are specific to this build, however the initial idea and credit goes to LoCoCNC's [Wire Grommet Mod](https://github.com/VoronDesign/VoronUsers/tree/master/printer_mods/LoCoCNC/wire_grommets).
  - Wire grommet for passthrough of Tircowns ERCF easy board to the ERCF
  - PTFE grommet for passthrough of PTFE from top deck panel to top panel
  - PTFE and Umbilical grommet for passthrough of PTFE and Wires to the toolhead
  - Wire grommet for the Z-chain wires
  - Wire grommet for the wires trough the bottom panel to the bottom of the chamber
- The Z-chain uses the original Voron V2.4 mounting brackets, they are simply reversed to run it from the top to the A drive
- I'm using a Raspberry Pi 4b, directly attached to the Waveshare 4.3" LCD screen, the BTT Octopus v1.1 and Tircown's ERCF Easy Board. I use TMC 2209 as stepper driver for everything.
- In the chamber, to tidy up the wiring under and behind the heated bed, I'm using a PCB as a central connection point.
- As the standard DoomCube was envisioned, I have my PSU and SSR on the underside and the controller boards in the top compartiment. This way high and low voltage are seperated and you have easy access to the controller boards.
- All electronics in the lower and upper compartment are placed on DIN rails so I never need to change holes in the panels to mount them. The DIN Rails are not screwed to the panel (like on the Voron V2.4, but are attached with screws (on top of the skirts base) to the extrusion.
- I use Phoenix UT 2,5 terminal blocks for wire management, this is optional.

|Mod|Creator|
|:---:|:---:|
[Heated Bed PCB](https://github.com/mvieleers/Voron-V2/tree/main/PCB/Heated%20Bed)|mvieleers
[V2_Octopus_Mount](https://github.com/walttriano/V2_Octopus_Mount)|walttriano
[ERCF Easy Board Mount](https://github.com/Tircown/ERCF-easy-brd/tree/main/mods/DIN%20mount)|mvieleers

### Printed Parts
Part|STL Origin|QTY
|:---:|:---:|:---:|
UHP-500-55 DIN Rail Mounts (2 parts)|[This Mod](STL/Electronics/DIN%20Mounts)|1
LRS-200-24 DIN Rail Mounts (2 parts)|[Voron Standard](https://github.com/VoronDesign/Voron-2/tree/Voron2.4/STLs/VORON2.4/Electronics_Compartment/DIN_Brackets)|1
ERCF Wire Grommet (4 parts)|[This Mod](STL/Electronics/Grommets)|1
PTFE Wire Grommet(4 parts)|[This Mod](STL/Electronics/Grommets)|1
PTFE and Umbilical Grommet (4 parts)|[This Mod](STL/Electronics/Grommets)|1
Z-Chain Grommet (4 parts)|[This Mod](STL/Electronics/Grommets)|1
Heated Bed Grommet (4 parts)|[This Mod](STL/Electronics/Grommets)|1

### Hardware
Hardware|Part|QTY|Remarks
|:---:|:---:|:---:|:---:
Controllers
||[Raspberry Pi 4b](https://www.raspberrypi.org/products/raspberry-pi-4-model-b/)|1|
||[BTT Octopus Pro v1.0 with TMC5160PRO](https://www.aliexpress.com/item/1005003349571423.html?spm=a2g0s.9042311.0.0.2f5a4c4dtMxMBK)|1|
||[Tircown's ERCF Easy Board with TMC 2209](https://github.com/Tircown/ERCF-easy-brd)|1|
4.3" LCD|[Waveshare 4.3" LCD DSI](https://www.waveshare.com/4.3inch-dsi-lcd.htm)|1|The Raspberry Pi can be screwed to the LCD screen
Power Inlet|[Schaffner FN-286](https://www.digikey.nl/product-detail/en/schaffner-emc-inc/FN286-1-06/817-1928-ND/1997125?productid=1997125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)|1
PSU|[Meanwell LRS-200-24](https://www.digikey.nl/product-detail/en/mean-well-usa-inc/LRS-200-24/1866-3332-ND/7705026?productid=7705026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)|1|
PSU HV|[Meanwell UHP-550(r)-55](https://www.arrow.com/en/products/uhp-500-55/mean-well-enterprises)|1|
SSR|[Omron G3NA](https://industrial.omron.nl/nl/products/G3NA-210B-UTU-5-24VDC)|1|
DIN Mount for SSR|[Omron G3NA DIN Rail Mount](https://nl.rs-online.com/web/p/relay-sockets/8278478/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)|1|
Terminal Blocks|[Phoenix Contact UT2,5](https://www.phoenixcontact.com/online/portal/nl/pxc/product_list_pages/!ut/p/z1/xVTfT9swEP5beMij43PjpOYxVBOIAQN1gyYvke04rVnipI7bAH_9nG0vlSDVhKr5wb6Tvvvul-9wjlc4N3yv1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)|As much as you need|Several accessoires available
Wire Duct|[Phoenix Contact Wire Duct 2m](https://www.digikey.nl/product-detail/nl/phoenix-contact/3240187/277-5422-ND/2525008)|1|

## Enraged Rabbit Carrot Feeder

The ERCF is completely stock please refer to the amazing [Enraged Rabbit Project Github](https://github.com/EtteGit/EnragedRabbitProject) by EtteGit.

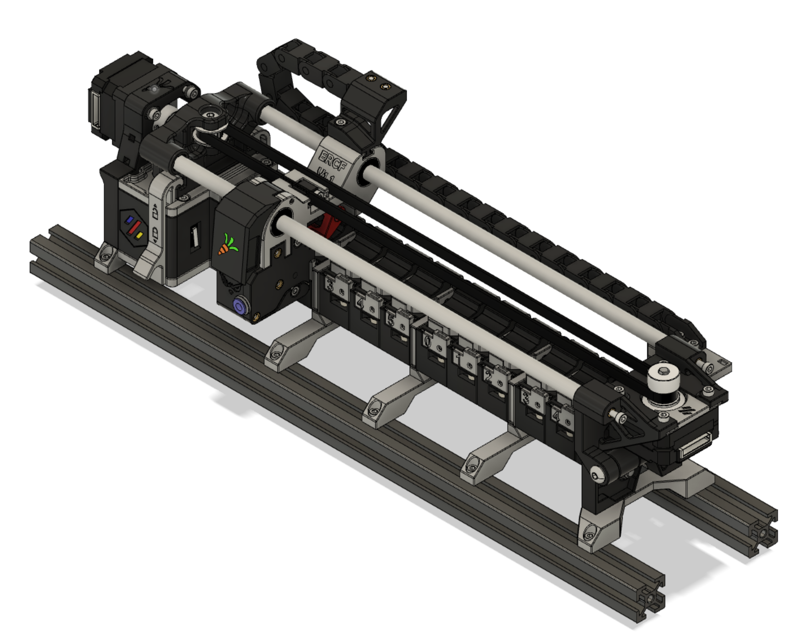
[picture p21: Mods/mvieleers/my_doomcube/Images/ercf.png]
ERCF


### Specifics
 - 12 Channel ERCF. Number of channels is irrelevant as I mount the ERCF to the extrusion and the extrusion is mounted to the top deck panel.

### Hardware
For mounting the frame to the Top Deck Panel you will need the following hardware:

Part|QTY
|:---:|:---:|
|[HFSB-2020-420](https://uk.misumi-ec.com/vona2/detail/110302683830/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)|2
|M5x10 BHCS|6|
|M3x8 SHCS|10|

#### A big thanks to all original creators for all their hard work to create all the Mods that were used in this DoomCube build. Always follow the links to their respective repos for the latest stls, and info on how to best make use of their mods.

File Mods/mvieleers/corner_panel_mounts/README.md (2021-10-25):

# Corner Panel Mounts

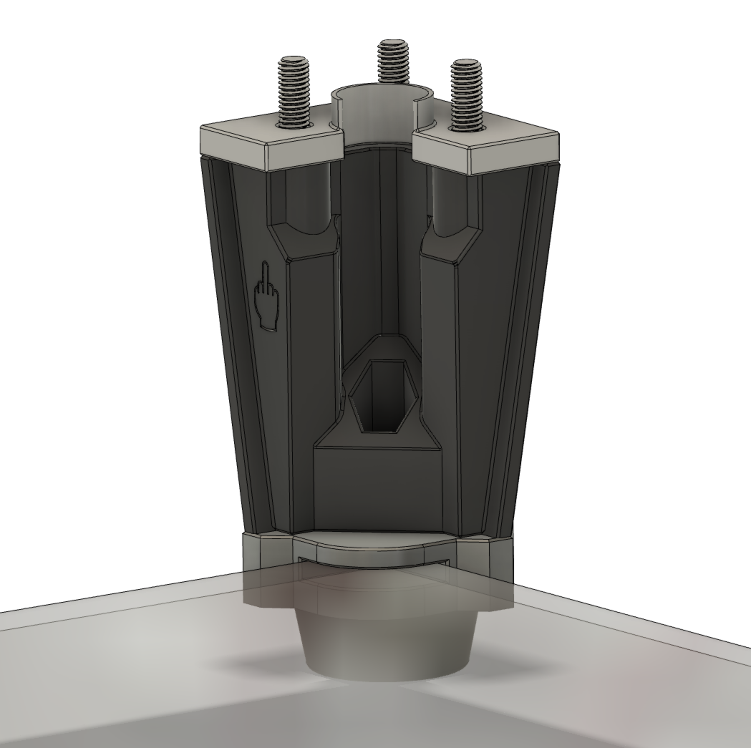
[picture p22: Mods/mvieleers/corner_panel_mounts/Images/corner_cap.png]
Corner Panel Mount

This mod replaces the square feet and the upper and lower corner caps from the original DoomCube.

The feet have been modded so that they each get 2 6x3 round magnets. The corner caps hold 2 magnets as well and they have a slot so they can go around the corners of the top and bottom deck panels. This way the deck panels are magnetically attached to the feet. When a 3mm panel is used, the panels align with the top of the skirts.

The bottom corner cap also has a cutout to hold an m5 hex nut, so the [Misumi Rubber Feet C-30-RK-3215](https://uk.misumi-ec.com/vona2/detail/110500157910/?HissuCode=C-30-RK-3215) can be attached to the corner feet.

### Hardware
Part|QTY
:---:|:---:
6x3mm round magnet (standard Voron)| 32
M5x16 BHCS| 4
M5 Locknut| 4
[Misumi Rubber Feet C-30-RK-3215](https://uk.misumi-ec.com/vona2/detail/110500157910/?HissuCode=C-30-RK-3215)|4

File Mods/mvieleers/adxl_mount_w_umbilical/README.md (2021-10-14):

# Galileo ADXL345 Chain Replacement with Umbilical Mount

This mod is an alteration of crag-h4k's mod to replace the chain mount on a Galileo extruder with an adxl345 mount. The original mod can be found [here](https://github.com/FrankenVoron/DoomCube-2/tree/main/Mods/crag-h4k/galileo-adxl345-chain-replacement).

The only thing I did to it, was to add two cutouts that allow two 3mm tie-wraps to be attached to the mount. This can be used to secure an umbilical to the X-carriage.

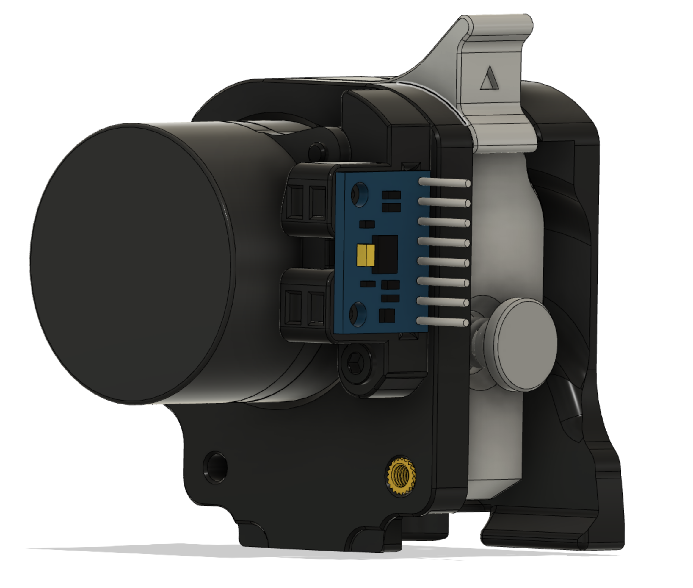
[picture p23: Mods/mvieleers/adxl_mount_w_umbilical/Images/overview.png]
ADXL Mount with Umbilical mount


### Hardware
Part|QTY
:---:|:---:
3x4x5 heatset insert (standard Voron)| 1
3mm tie-wrap|2

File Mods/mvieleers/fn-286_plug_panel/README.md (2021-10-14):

# FN286 Schaffner Plug Panel

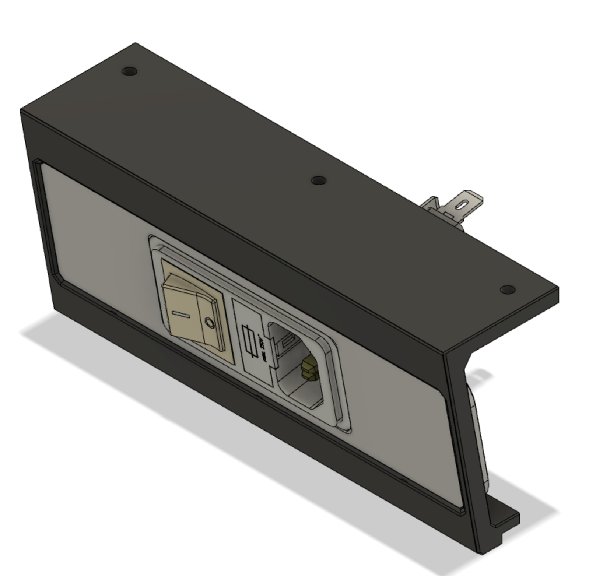
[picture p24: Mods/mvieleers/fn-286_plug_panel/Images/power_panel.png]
FN-286 Plug Panel

This mod replaces the inlay for the plug panel with an inlay that can hold the [Schaffner FN-286](https://www.digikey.nl/product-detail/en/schaffner-emc-inc/FN286-1-06/817-1928-ND/1997125?productid=1997125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).

The Skirt itself is not altered.

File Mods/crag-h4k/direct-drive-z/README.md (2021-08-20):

# direct drive z

Based on joshmurrah's direct drive mod for the v2.4 - adapted to DOOM! 

### Notable Features

- reduces required parts and complexity of typical z drive motor units
- slot in the corner of the motor mount to give space for cabling that is passed through the 4040 extrusion frame
- GT2 grub screw access hole
- the key-baks gives a nice combination of jank and ingenuity ;)

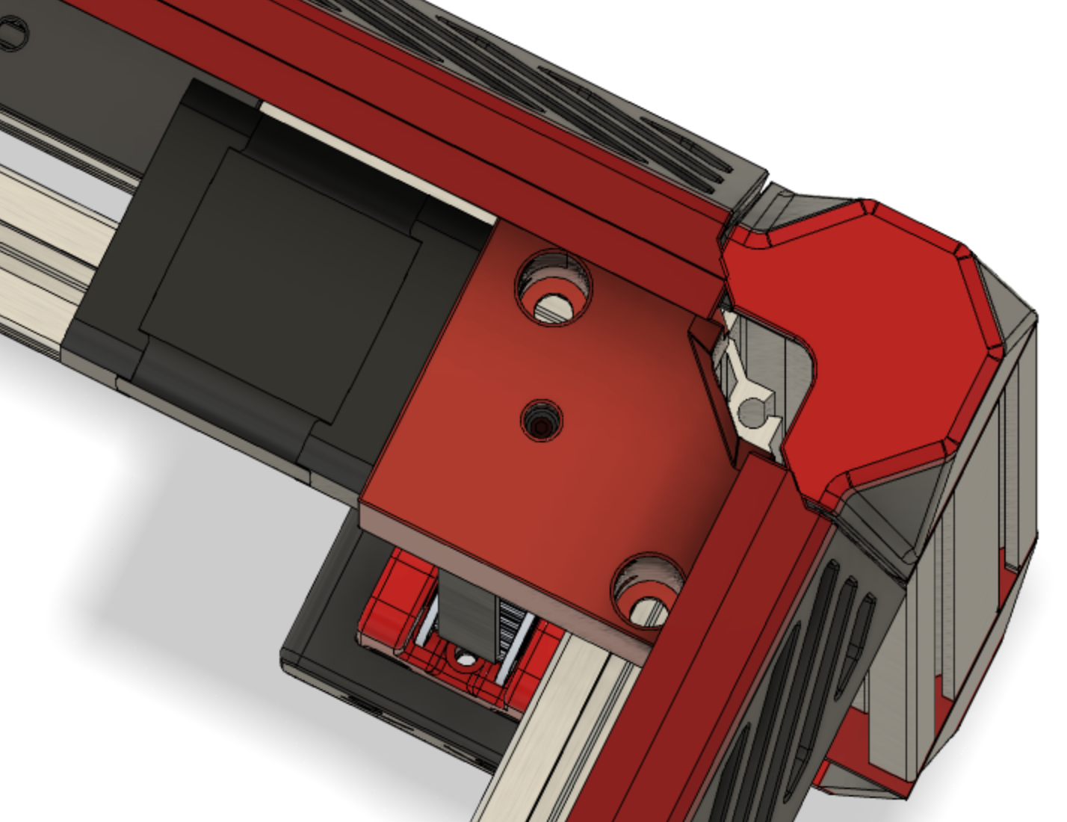
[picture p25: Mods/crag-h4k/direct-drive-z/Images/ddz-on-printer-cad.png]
top view

 
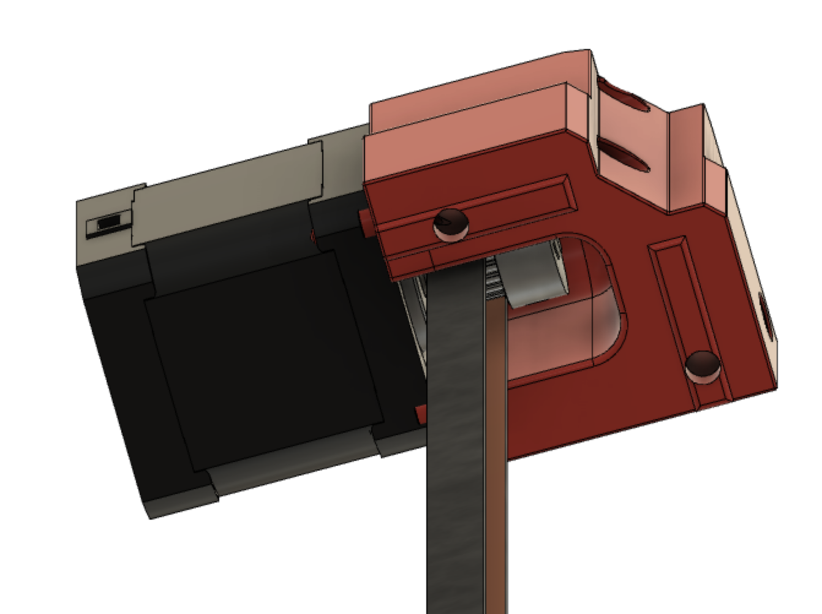
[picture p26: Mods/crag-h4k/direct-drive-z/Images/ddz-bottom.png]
bottom view




## Tips

- the space between the motor and the DOOM cubes panel mounting is tight, may want to use m3 bhcs for mounting the panel
mounts to the extrusion
- you'll probably want to have two key-baks on your build; if so, double the amount in the key-bak holder's BOM below

## BOM

### direct drive z

---
| part |  notes | quantity | source |
| --- | --- | --- | --- |
| NEMA17 Stepper  | I am using 1.8 deg steppers, .9 deg steppers probably better. | 4 | [Amazon](https://www.amazon.com/STEPPERONLINE-Stepper-Bipolar-Connector-compatible/dp/B00PNEQKC0)|
| GT2 20T 10mm width 5mm bore pulley | if using 6mm belts get the 7mm width version | 4 | [Amazon](https://www.amazon.com/WINSINN-Aluminum-Synchronous-Timing-Printer/dp/B07BT6N12L)  |
| Gates GT2 9mm belts | can use 6mm belts | length depends on build size |  |
| m3x8 shcs  | for mounting motor to mount | 16 |  |
| m5x10 bhcs | for mounting to extrusion | 8 |  |
| m5 roll-in t-nuts | for mounting to extrusion | 8 |  |
---

### key-bak holder

---
| part |  notes | quantity | source |
| --- | --- | --- | --- |
| keybak super48 | the beefy version - 28" Kevlar Cord / 20 oz. Force | 1 | [Amazon](https://www.amazon.com/gp/product/B01CQLJ8I0) |
| 604uu bearing  | key-bak's cord rolls on this | 1 | [Amazon](https://www.amazon.com/HUABAN-4x13x4mm-U-Shaped-Extruder-Bearings/dp/B076D67T6V) |
| m4x20 bhcs or shcs  | for 604uu bearing | 1 |  |
| m5x30 bhcs | for mounting to extrusion | 2 |  |
| m5x10 bhcs | for mounting retainer to extrusion | 1 |  |
| m5 roll-in t-nuts | for mounting retainer and keybak holder to extrusion | 3  |  |
---

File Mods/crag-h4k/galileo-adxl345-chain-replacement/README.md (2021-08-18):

# galileo adxl345 chain replacement

Replaces the Galileo extruders's chain mount with a dedicated mount for a adxl345.

## Images



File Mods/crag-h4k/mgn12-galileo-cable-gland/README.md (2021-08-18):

# mgn12 galileo compatible cable gland mount

Simple cable gland mount for mgn12 x-axis mod and Galileo extruder.

## Images







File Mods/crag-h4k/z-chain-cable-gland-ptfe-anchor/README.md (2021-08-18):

# z chain m12 gland ptfe anchor

Simple a cable gland mount and 4mm PTFE tube pass-through for upper Z chain anchor - attempts to preserve z-axis build volume.

## Images
















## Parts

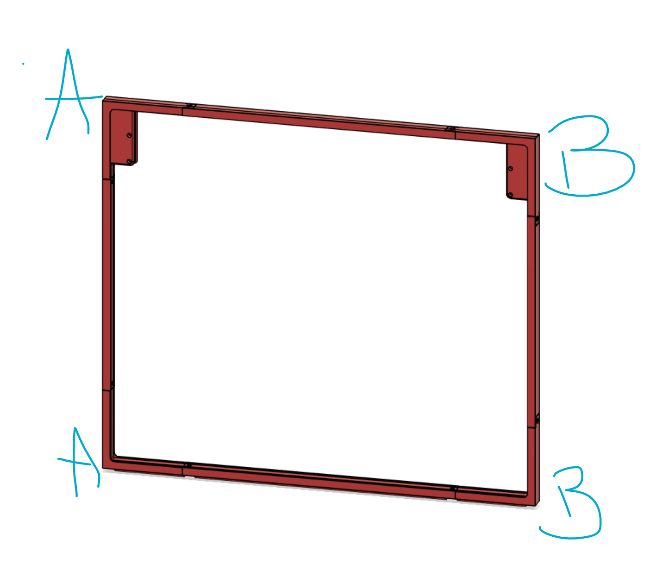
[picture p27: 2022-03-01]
Mods/KayosMaker/Tip_In_Magnetic_Panels/STLs/350PanelFrames/sides_rear_frames/frame_parts_pic.png

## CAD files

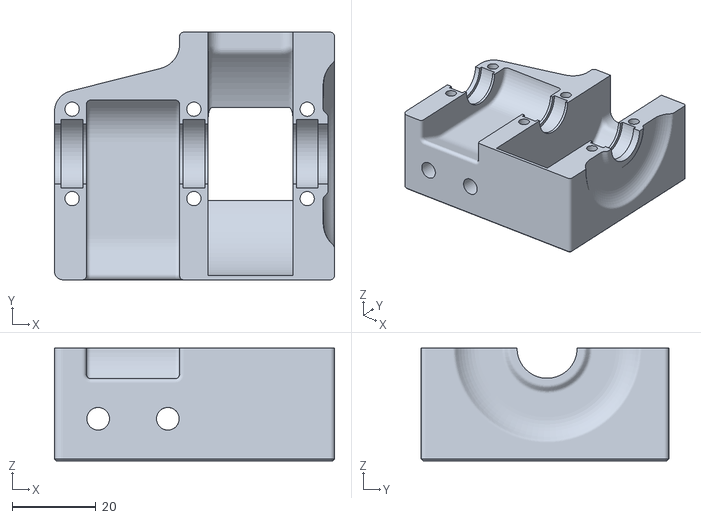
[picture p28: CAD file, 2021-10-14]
STLs/Z_Drives/z_drive_main_a_x2_doom.stl
66.7 x 59.0 x 26.8

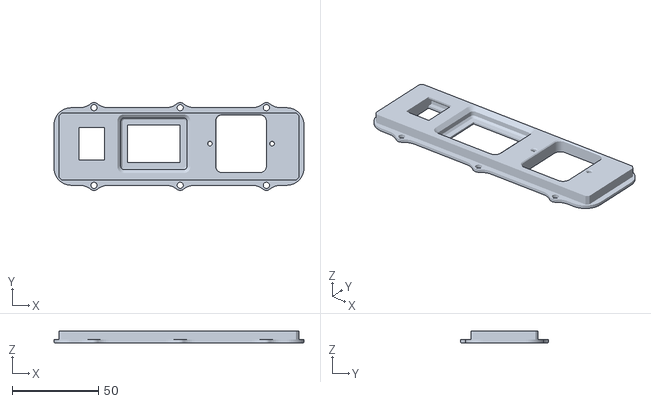
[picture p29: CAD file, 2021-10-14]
STLs/Skirts/[a]_power_panel_skirt_frame_insert_filtered_mains_keystone.stl
145.0 x 51.0 x 7.00

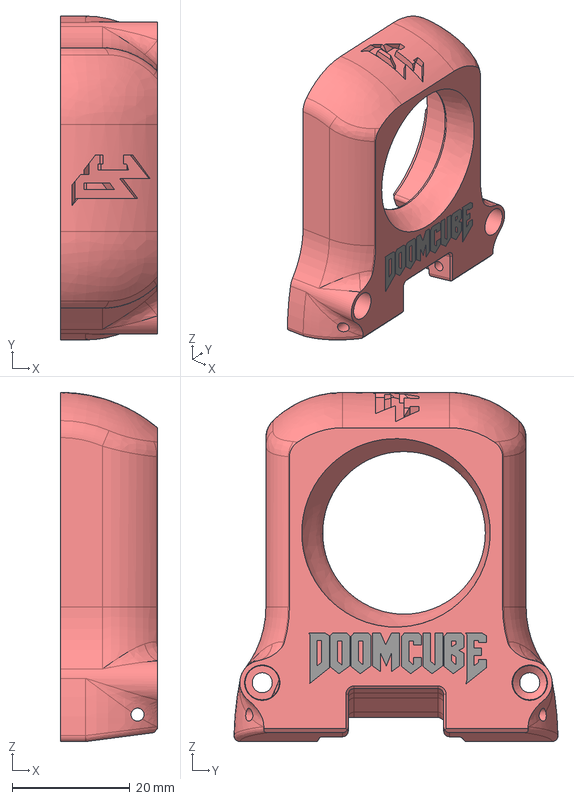
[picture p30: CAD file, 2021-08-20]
CAD/Doomcube AB Blower Housing/BlowerHousing.step
16.5 x 55.0 x 59.3 mm

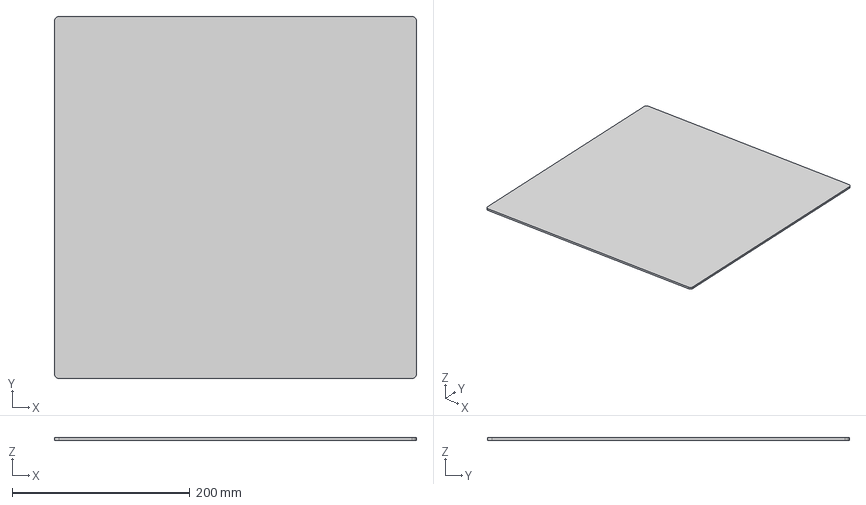
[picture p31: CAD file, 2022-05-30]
CAD/Doors and Side Panels/250/doom_250_cover_topbottom_x2.step
407.0 x 407.0 x 3.00 mm

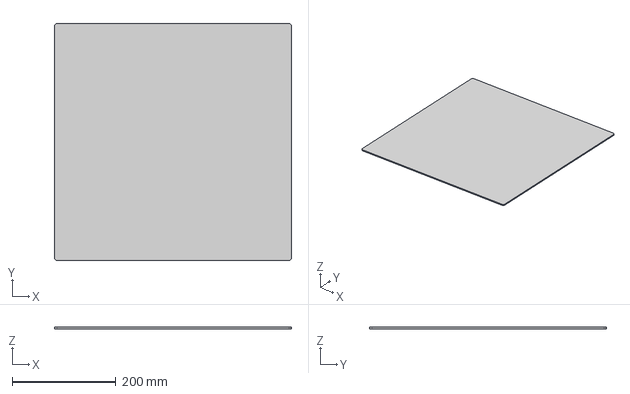
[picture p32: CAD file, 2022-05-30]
CAD/Doors and Side Panels/300/doom_300_cover_topbottom_x2.step
457.0 x 457.0 x 3.00 mm

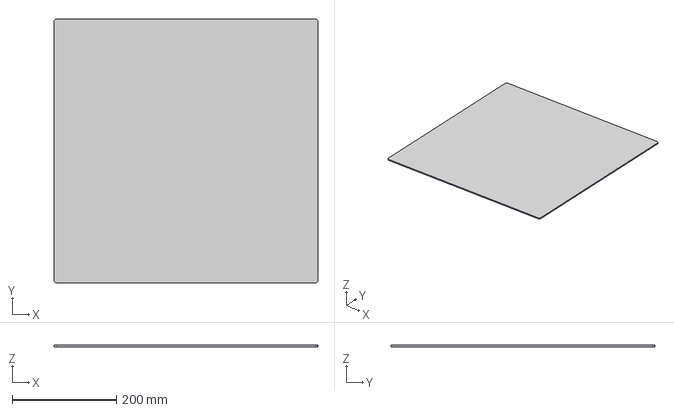
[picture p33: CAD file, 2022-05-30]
CAD/Doors and Side Panels/350/doom_350_cover_topbottom_x2.step
507.0 x 507.0 x 3.00 mm

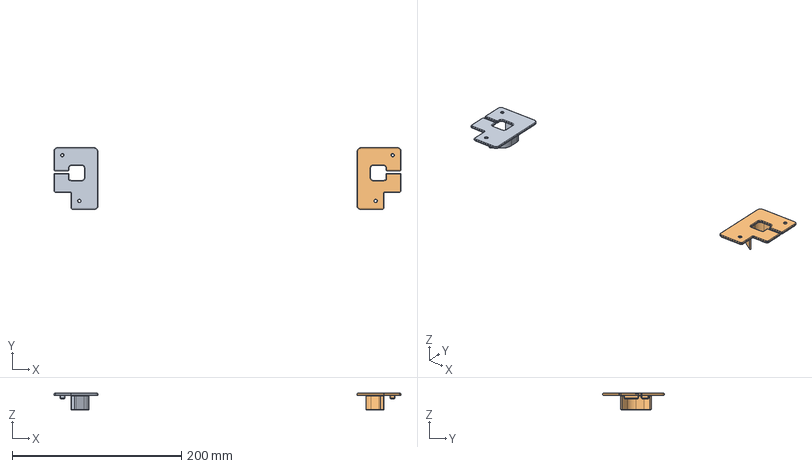
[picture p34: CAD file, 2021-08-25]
CAD/Doors and Side Panels/z_belt_cover_non_reflectix.step
410.3 x 73.0 x 19.6 mm

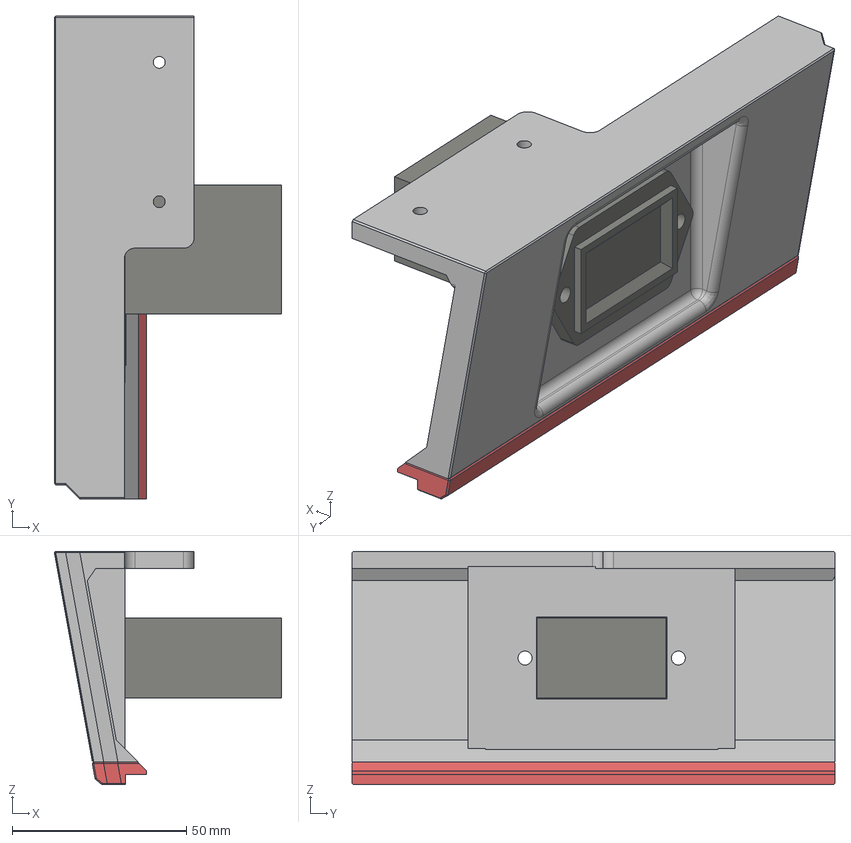
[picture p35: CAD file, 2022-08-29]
CAD/Skirts/HourMeterFor300.step
65.3 x 138.6 x 67.0 mm
SideSkirt (1)
HourCounter

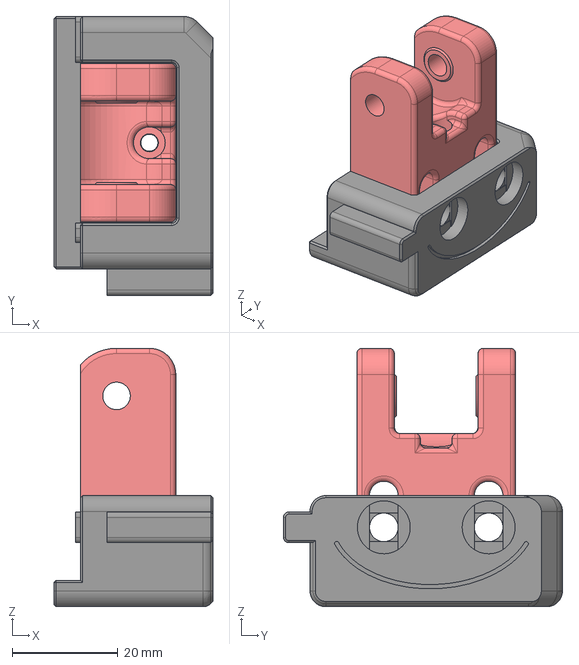
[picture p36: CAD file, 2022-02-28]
CAD/Z Idlers/Z Idler.step
30.0 x 52.7 x 48.8 mm

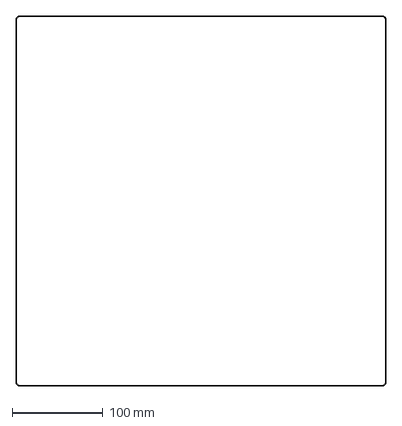
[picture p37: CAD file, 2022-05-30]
DXFs/250/cover_panel_topbottom_x2.dxf
407.0 x 407.0 mm

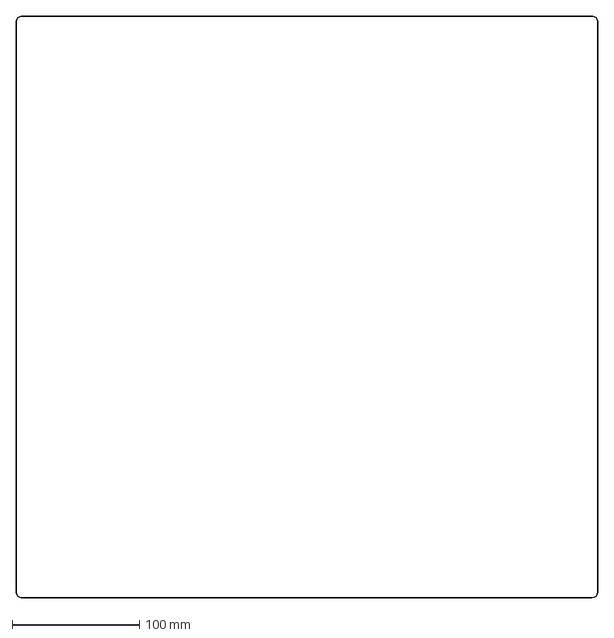
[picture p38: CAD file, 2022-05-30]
DXFs/300/cover_panel_topbottom_x2.dxf
457.0 x 457.0 mm

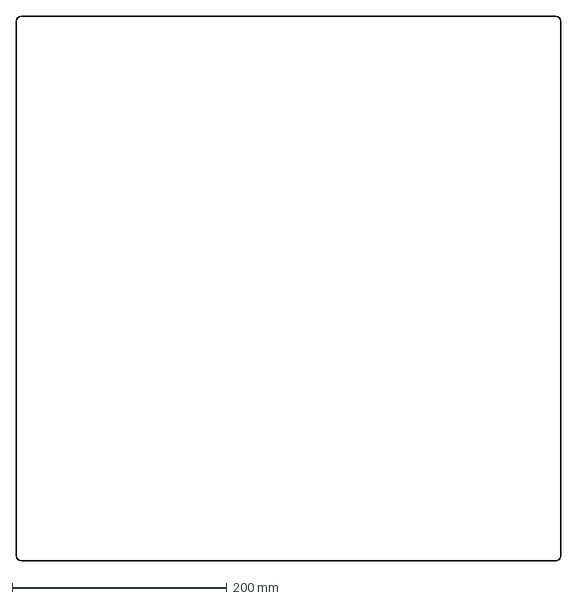
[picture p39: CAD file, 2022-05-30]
DXFs/350/cover_panel_topbottom_x2.dxf
507.0 x 507.0 mm

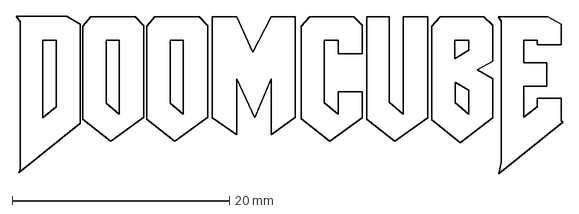
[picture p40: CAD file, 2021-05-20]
DXFs/Logos/DOOMCUBE.dxf
50.4 x 14.5 mm

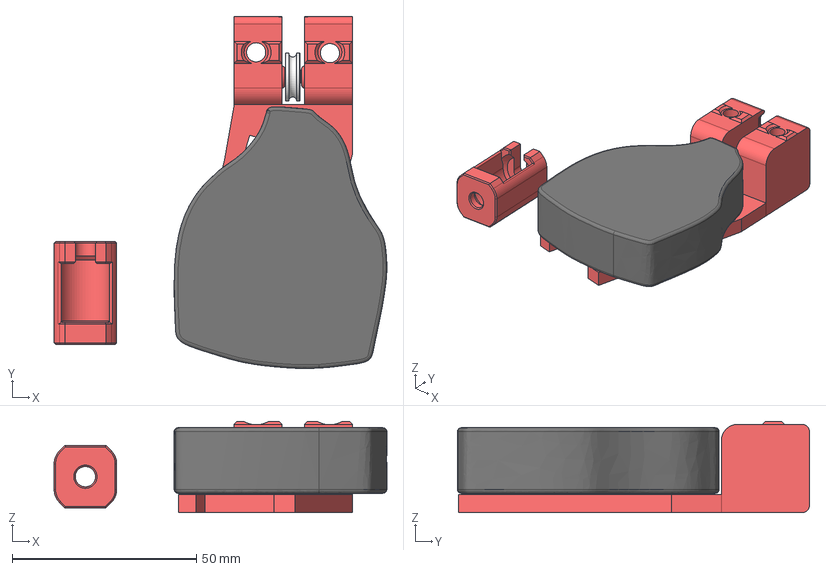
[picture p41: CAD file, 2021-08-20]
Mods/crag-h4k/direct-drive-z/CAD/top mounted keybak super48 604uu.step
90.4 x 95.6 x 24.8 mm
main body
keybak super48 v1
keybak-AB-retainer.stl
M4x20 v1 v1

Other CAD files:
STLs/Z_Drives/z_drive_main_b_x2_doom.stl
Mods/crag-h4k/direct-drive-z/STLs/keybak-AB-retainer.stl
Mods/crag-h4k/galileo-adxl345-chain-replacement/CAD/Galileo adxl mount v26.step
Mods/crag-h4k/galileo-adxl345-chain-replacement/STLs/galileo-adxl345-mount.stl
CAD/Corners/RoundedCorners.step
CAD/Corners/SquareCorners.step
CAD/Skirts/250BlankSkirts.step
CAD/Skirts/300BlankSkirts.step
CAD/Skirts/350BlankSkirts.step
CAD/Skirts/CenterSkirtDisplayWithAccent.step
CAD/Skirts/HexagonSkirts.step
CAD/Skirts/HourMeterFor350.step
CAD/Skirts/PowerPanelCenterSkirt.step
CAD/Skirts/SlottedSkirts.step
CAD/Z belt cover/z_belt_cover_reflectix_v26.f3d
DXFs/250/deck_panel_bottom_x2.dxf
DXFs/250/deck_panel_top_x2.dxf
DXFs/250/door_x2.dxf
DXFs/250/side_back_x6.dxf
DXFs/300/deck_panel_bottom_x2.dxf
DXFs/300/deck_panel_top_x2.dxf
DXFs/300/door_x2.dxf
DXFs/300/side_back_x6.dxf
DXFs/350/deck_panel_bottom_x2.dxf
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

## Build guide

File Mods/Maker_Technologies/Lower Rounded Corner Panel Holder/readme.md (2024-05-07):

Modified the Lower Rounded corner parts to keep the bottom panel in place. I used a 3mm thick ABS panel and it worked well. Should be compatible with everything else without any problem.
Former version attached for your convenience.

As always, let know of any feeback and suggestions...

-Dom Dell Optiplex 7000 #0675

[lower corner rounded cap.zip](https://github.com/ddellant/DoomCube-2/files/9932078/lower.corner.rounded.cap.zip)

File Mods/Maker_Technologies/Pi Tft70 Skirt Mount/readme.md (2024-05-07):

I have created a simple Pi TFT70 Mount that attaches at the front top center skirt (like in the CAD). I was able to reuse the screws that came with my tft70. Think they are m2.5 (?). It creates a clean and sleek way to mount the tft while hiding the ribbon cable completetly. I have been using mine for months now and have had no issues. It is very important to keep this top bay cool so I do reccomend some active cooling.

As always, reach out if you have any questions...

-Dom Dell Optiplex 7000 #0675

[Doom case.zip](https://github.com/ddellant/DoomCube-2/files/9932102/Doom.case.zip)

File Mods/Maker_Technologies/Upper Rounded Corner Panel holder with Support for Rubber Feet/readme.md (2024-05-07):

As the stock design does not support a way to hold the top panel down. I have created this part to solve this. I tried to keep it compatible with everything else found on an OEM DOOM. 
This model will also support putting rubber feet on the upper panels. This is for maitanence purposes only, keeps the printer off a ground a bit more too when flipped upside down. 
You will need to insert m3 heat set inserts into the holes of upper_corner. Then you can secure the caps with m3 hardware. The feet can be installed using an M5 screw.

I have included former versions of the models and their cad files for your convenience. I would reccomend only using V5 if V4 does not look good when printed. V5 has been altered to print better at the cost of some dimentional discrepencies. I am using V4 on my printer, V2.4515.

[For Release.zip](https://github.com/ddellant/DoomCube-2/files/9871357/For.Release.zip)

Feedback is always apprciated. HMU!

  -Dom Dell Optiplex 7000#0675

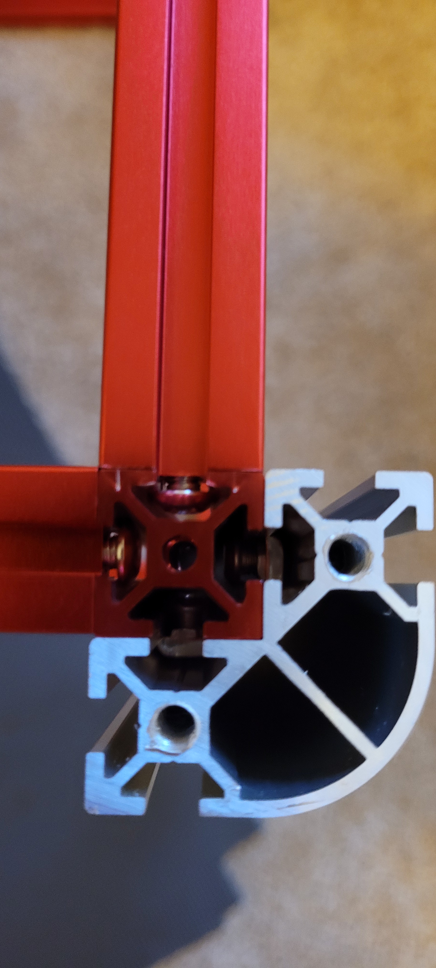
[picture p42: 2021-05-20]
Images/BuildPhotos/404020-1.jpg

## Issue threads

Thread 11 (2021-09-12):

Does this design not take into account the installation of the fan in the electronics compartment?

poloniumn, 2021-09-12:
This is a very nice design, I really like it, but I downloaded and checked the CAD model and found that the skirt is not designed with a fan, how is the cooling of the motherboard done? Install the fan directly on the motherboard?

hartk1213, 2021-09-12:
currently there isnt an official fan mount in the skirts, i just have a fan stuck with vhb tape blowing on the drivers ...i want to eventually install a blower fan up there i just havent gotten around to it

poloniumn, 2021-09-12:
Thank you.

Looks like I can print a motherboard fan bracket internally to dissipate the heat, which isn't difficult

One more small question, will there be any other changes in the near future, I'm going to start upgrading my voron, I don't want it to become obsolete in the middle of production

poloniumn, 2021-09-12:
One more question, I noticed that the machine does not have an exhaust like voron, he is a completely closed machine? How to solve the unpleasant smell of ABS?

hartk1213, 2021-09-12:
Never more micro is what I have installed in mine to deal with smell

Closed 2021-09-13.

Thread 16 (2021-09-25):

TDL #1  alter skirts to suit common screw lengths

KayosMaker, 2021-09-25:
to do list #1
the skirts currently require a washer to use common m3 screw sizes.  we need to add a raised ring around each hole, or simply extrude the entire surface 1mm or so.  its simple, but a lot of work with 3 sets of skirts and accessory panels.

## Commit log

2021-03-30 added doors and side panels
    [doom_250_side_panel_and_door.f3d, doom_300_side_panel_and_door.f3d, doom_350_side_panel_and_door.f3d]
2021-03-30 Add Z updates for DC and display
    [VORON2 v2.4 Assembly - Final_Z Belt Drive Doom.f3d, [a]_center.stl, [a]_z_tensioner_bracket_x4_9mm_dc.stl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]
2021-03-31 updated step files for 250,300,350 Door and Side panels
    panels clips are now designed for 3mm panels,
    panel clips are also now designed with clearance for the Z rail
    panels are also all the correct dimensions, DXF files are to follow soon
    also added skirt flanges for the doors for 250, and 350
    [doom_250_side_panel_and_door.f3d, doom_300_side_panel_and_door.f3d, doom_350_side_panel_and_door.f3d]
2021-04-01 Added Deck panles for 250,300,350
    added Deck, Side, and Door Panel DXFs for 250,300,350, updated CAD files to now include deck panels, exported all files to STL and oriented all exported STLs for printing.
    [[a]_center_skirt_door_flange_x2.stl, [a]_deck_panel_inner_frame_edge_front_back_x8.stl, [a]_deck_panel_inner_frame_edge_side_x8.stl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]
2021-04-06 Added stls for rounded Doom Corners
    [[a]_bottom_corner_cap_x4.stl, [a]_corner_base_accent_x8.stl, [a]_upper_corner_DClogo_x4.stl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]
2021-04-07 added tools, toolhead, and gantry files
    [[a]_blower_housing_front_DC_x1.stl, [a]_cable_cover_doom.stl, blind_joint_jig_4040.stl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]
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2021-04-22 changed file name to update the correct qty to be printed
    [[a]_side_and_deck_panel_inner_frame_center_x14.stl]
2021-04-26 added Square 4040 corner pieces
    Upper and Lower corners have been added as well as the accent pieces to go with them. The skirts will come soon , just need to finish up a few things
    [[a]_corner_base_accent_x8.stl, [a]_lower_corner_cap_x4.stl, [a]_upper_corner_cap_x4.stl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]
2021-04-26 moved z chain mount to the correct spot
    [z_chain_top_anchor.stl]
2021-05-03 Update side_back_x6.dxf
    fixed dxf for side_back panel for 250
    [side_back_x6.dxf]
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2021-05-03 update corner caps to fit with skirts better
    [[a]_lower_corner_cap_x4.stl, [a]_upper_corner_cap_x4.stl]
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2021-05-07 added blank skirts for 250-350 , added bruag patter skirts for 300 (250,350 will be up soon),added dual color display panel, added plug panel. as well as 300 side skirt hour counter
    [250BlankSkirts.step, 300BlankSkirts.step, 350BlankSkirts v2.step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]
2021-05-14 fix orientation
    [power_panel_skirt_frame.stl]
2021-05-20 added logo dxf files as well as photoshop file and font files to make other logos etc.
    [DCOverlapStaggard.dxf, DOOMCUBE.dxf]
2021-06-03 updated lower corner and display to match skirts
    [[a]_frame_accent.stl, frame.stl, lower_corner_x4.stl]
2021-06-05 added CAD files for square and rounded corner pieces, as well as updated the rounded to the newest style with the wire channels
    [RoundedCorners.step, SquareCorners.step, [a]_corner_base_accent_x8.stl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]
2021-06-05 added standard hexagon skirts for 250,300,350
    [250_side_skirt_mirror_x8.stl, 250_side_skirt_x8.stl, 300_side_skirt_mirror_x8.stl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]
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2021-06-22 added zidlers, zdrives, and updated round corner caps
    [Z Idler.step, [a]_upper_corner_cap_x4.stl]
2021-08-09 z idler update
    create clearance between idler body and doom bottom panels
    [Z Idler.step, z_tensioner_bracket_a_x2_dc.stl, z_tensioner_bracket_b_x2_dc.stl]
2021-08-10 move files to correct locations
    remove z drive cad from stl folder and place in its own folder in cad
    remove z idlers from z drive cad folder, place into their own z idler folder
    [VORON2 v2.4 Assembly - Final_Z Belt Drive Doom.f3d, Z Idler.step]
2021-08-12 add doomcube blower housing and hour meter skirt panel cad
    add some missing cad
    [BlowerHousing.f3d, HourMeter350.f3d]
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2021-08-17 update cad and add step file
    -more organization of cad
    -klicky probe installed on 2 gantries it is compatible with
    -sexbolt endstop installed
    -bed placement corrected
    -add zipped step file to complete cad folder
    -update readme with cad details
2021-08-18 first commit, adds cad, md, stls, and images to ./Mods/crag-h4k
    [Galileo adxl mount v26.step, Z anchor 10x11 chain 12mm cable gland ptfe.step, galileo-adxl345-mount.stl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]
2021-08-18 the commit adds direct-drive-z mod, and adds more comprensive macOS and ide garbage/temp files to .gitignore
    [ddz-motor-top-mount-2x.stl, ddz-motor-top-mount-MIRROR-2x.stl, keybak-AB-retainer.stl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]
2021-08-19 Component CAD update
    -fix holes to be correct sizes
    -added missing chamfers(or ones i thought should be there)
    -fixed some minor geometry issues
    [250BlankSkirts.step, 300BlankSkirts.step, 350BlankSkirts.step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]
2021-08-25 this commit adds top mounted z belt covers for non reflectix top deck panels
    [[a]_z_belt_cover_non_reflectix_A_x2.stl, [a]_z_belt_cover_non_reflectix_B_x2.stl, z_belt_cover_non_reflectix.step]
2021-08-25 fixed print orientation
    [[a]_z_belt_cover_non_reflectix_A_x2.stl, [a]_z_belt_cover_non_reflectix_B_x2.stl]
2021-08-27 add more cad
    -add eddies belt cover
    -add folder for my panel frame mod and add work in progress files to it:
    -edited doom corners to not interfere with panel frame corners
    -added frame generator i'm using to build up each panel type(and generate it at different sizes)
    [RoundedCorners.step, SquareCorners.step, panel frame builder v10.f3d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]
2021-08-31 big stl update
    -add stls for optional skirts in cad
    -update stl's for any cad that was touched up
    -remove redundant 12864 skirt section
    [250_blank_side_skirt.stl, 250_blank_side_skirt_mirror.stl, 250_bruag_side_skirt.stl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]
2021-09-03 Adding CAD, Drawings, PCB, DXF, STL
    Initial upload of all files
    [Heated Bed.step, MGN12_rail_guide_x2.stl, MGN12_xy_joint_left_lower_pinned.stl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]
2021-09-13 upload images
    3 images uploaded
    [3center_skirts.3mf, 3center_skirts_bottom.3mf, 4left_skirts.3mf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]
2021-09-13 Updated file names and drawings
    [heated_bed.step, panel_bottom.dxf, panel_bottom_deck.dxf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]
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2021-09-18 STL orientation fixed
    [[a]_grommet_bed_bottom_a.stl, [a]_grommet_bed_bottom_b.stl, [a]_grommet_bed_top_a.stl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]
2021-09-21 Update skirt_right_x4.stl
    Fixed toolpath outside build area
    [skirt_right_x4.stl]
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2021-10-05 fixed orientation of lower corner pieces
    [lower_corner_x4.stl]
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2021-10-12 Change slot cover brand
    Replace Misumi slot cover with aliexpress slot covers.
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2021-10-25 Corner Caps
    Moved locknut from foot to cap
    [[a]_bottom_panelmount_x4.stl]
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2021-10-26 Added bottom extrusions to use std hole positions
    Added bottom extrusions to go back to the original hole positions. Benefit: added stability
2021-10-26 Added bottom extrusions
    Back to normal hole position
    [[a]_flange_bottom_center_x4.stl, [a]_flange_center_8x.stl, [a]_flange_left_x4.stl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]
2021-11-04 Updated electonics
    Added 55V PSU and updated layout
    [uhp_psu_bracket_clip.stl]
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2022-02-12 renamed skirt files
    added _x6/_x8 as appropriate based on existing examples to make the naming more consistent between skirt designs
    [250_blank_side_skirt_mirror_x8.stl, 250_blank_side_skirt_x8.stl, 250_bruag_side_skirt_mirror_x8.stl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]
2022-02-12 fixed typo in name
    fixed incorrect space added before _
    [250_slotted_side_skirt_mirror_x8.stl]
2022-02-26 Fan and LCD Skirt changes
    Added a Fan Skirt for 60x60x20 fans.
    Beefed the screw holes to mount the LCD to the skirt.
    [skirt_top_center_x2.stl, skirt_top_center_x3.stl, skirt_top_fan.stl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]
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2022-03-01 begin setting my tip in panel mod in place
    [RoundedCorners.step, SquareCorners.step, [a]_corner_base_accent_x8.stl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]
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2022-03-20 forgive my crappy cat skillz
    Added top / bottom cover .step and .dxf panels for all doom cube sizes.
    renamed deck_panel_top.dxf to indicate quantity for complete build (x2)
    [cover_panel_topbottom_x2.dxf, deck_panel_bottom_x2.dxf, deck_panel_top_x2.dxf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]
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2022-08-29 Add files via upload
    Added back the 300 hour meter skirt
    [hour_meter_frame_300.stl]
2022-09-13 replaced center skirt door flange with the correct one that has holes for the display skirt as well
    [[a]_center_skirt_and_display_door_flange_x2.stl, [a]_center_skirt_door_flange_x2.stl]
2022-11-18 fix extrusion image in README
2023-03-25 Adding panels holders with more clearance
    [Side_panels_with_more_clearance.f3d, [a]_horizontal_center_x2.stl, [a]_horizontal_side_mirror_x2.stl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]
2024-06-19 Update README.md
    replaced broken links with ones to same mod on mods.vorondesign.com; fixed busted pic of fancy round extrusion
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
